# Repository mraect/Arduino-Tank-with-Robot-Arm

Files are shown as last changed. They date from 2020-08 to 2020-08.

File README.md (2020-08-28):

# Arduino Tank with Robot Arm 

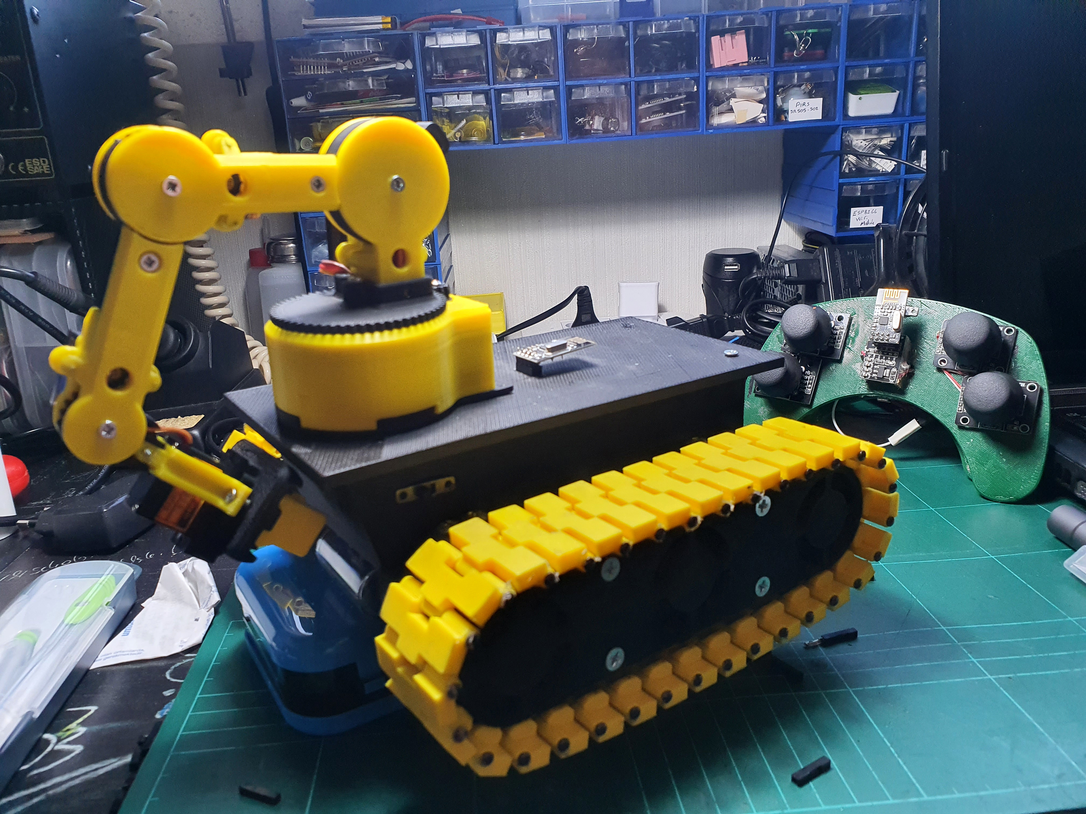
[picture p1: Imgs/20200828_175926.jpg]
ArduTankRobotArm


> For finished product photos, look "Imgs" folder.

# Needed Files;
  - For Robot Arm 3D files grab it from [Thingiverse - RobotArm3D][thingArm]
  - For Tank Threads 3D files grab it from [Thingiverse - Tank3D][thingTank]
  - For adapters and new chassis look "STL" folder
  - Code file look "Codes" folder
  - Need some sort of remote controller or raw Arduino attached nRF24L01 and some pots
  
  ### Folder Structure
  
| Folder | Description |
| --- | --- |
| Codes | Has 2 ino folder. One is for Main Arduino (KumandaAliciBasit) and other is for Robot Arm (RobotKolTekData)|
| Docs | PDF file which contains wiring diagram and explains data connection |
| Imgs | Images from finished project. Wiring photos, finished photos etc. |
| STL | 3D printer files which needed to make this project done |

# Needed Parts;
  - 2x Arduino Pro Mini
  - 4x DC geared Arduino motor
  - 5x 9g Servo (metal gear preferred)
  - 2x nRF24L01+ with breakout board
  - 3D printed files
  - Matek PDB or 12V to 5V buck converter (and more jumper wire)
  - M3 and M4 screws and nuts
  - 2mm x 30mm nails for treads
  - 2x Brushed ESC for tracks or one Brushed ESC which can control 2 motors separately.
  - 2S or 3S LiPo battery or 2 or 3 18650 LiIon battery
  - Jumper wires (female-female) to many of them :D
  - If you have 90° servos you need 2.2k resistors 2 for each servos

# Needed Tools;
  - Arduino IDE (v1.8.9 or higher) installed PC
  - 3D printer or slicing program fot STL files (Slic3r, Simple3D software etc.)
  - Screw driver
  - If you use PDB or you want to convert 90° servos to 180° servo, you need soldering iron
  - Hot glue gun for securing electronic parts
 
License
----

GNU GPLv3

[//]: # (These are reference links used in the body of this note and get stripped out when the markdown processor does its job. There is no need to format nicely because it shouldn't be seen. Thanks SO - http://stackoverflow.com/questions/4823468/store-comments-in-markdown-syntax)

   [thingTank]:<https://www.thingiverse.com/thing:972768>
   [thingArm]:<https://www.thingiverse.com/thing:2954381>

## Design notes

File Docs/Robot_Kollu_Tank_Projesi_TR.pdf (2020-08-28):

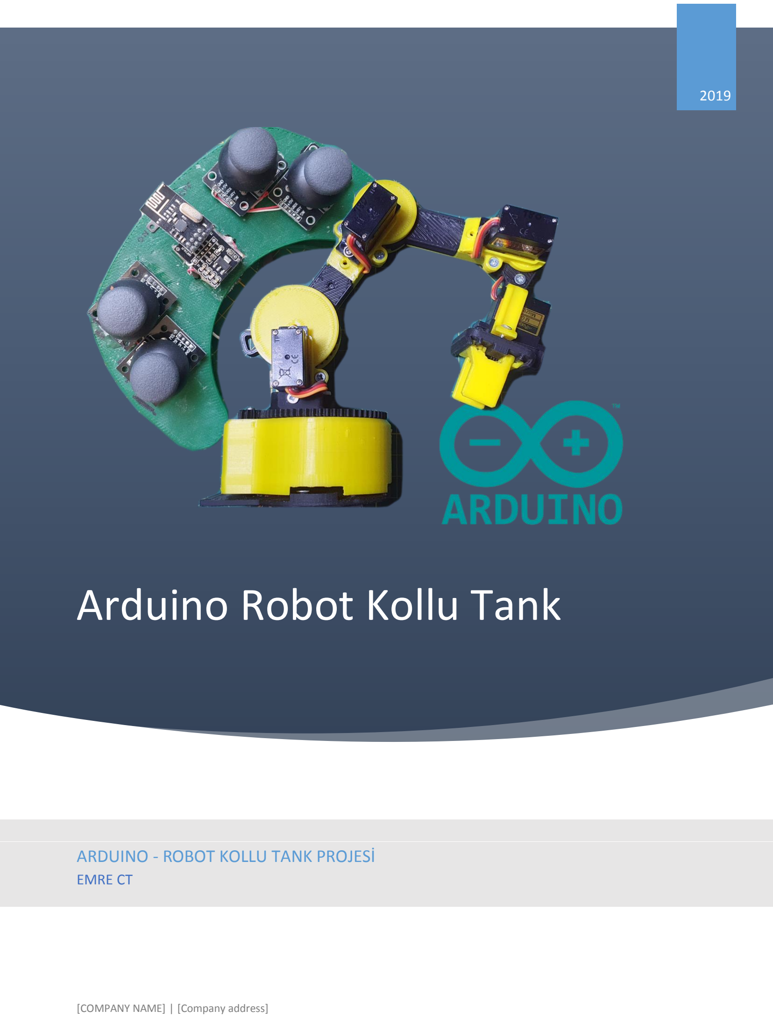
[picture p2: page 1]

# Arduino Robot Kollu Tank

2019

ARDUINO - ROBOT KOLLU TANK PROJESİ
EMRE CT
[COMPANY NAME] | [Company address]

Robot Kollu Tank Projesi

(Verici (Kumanda) Hariç)

## İçindekiler

Devre Elemanları

- 2x Arduino Pro Mini 5V/16Mhz
- 1x Matek PDB (Power Distribution Board) (Dahili 5V Buck Converterlı)
- 2x Brushless ESC
- 5x Servo 9g (MG90s Metal Gear)
- 1x NRF24L01+ Adaptör
- 1x NRF24L01+ Modül

Kısaltmalar

Ana Tank Kontrolörü Arduino Pro Mini (AR1 yada Main) (tankın önüne sabit olan Arduino)

Robot Kol Kontrolörü Arduino Pro Mini (AR2 yada Kol)

Brushless ESC (ESC)

nRF24L01+ (nRF)

Devre Şeması

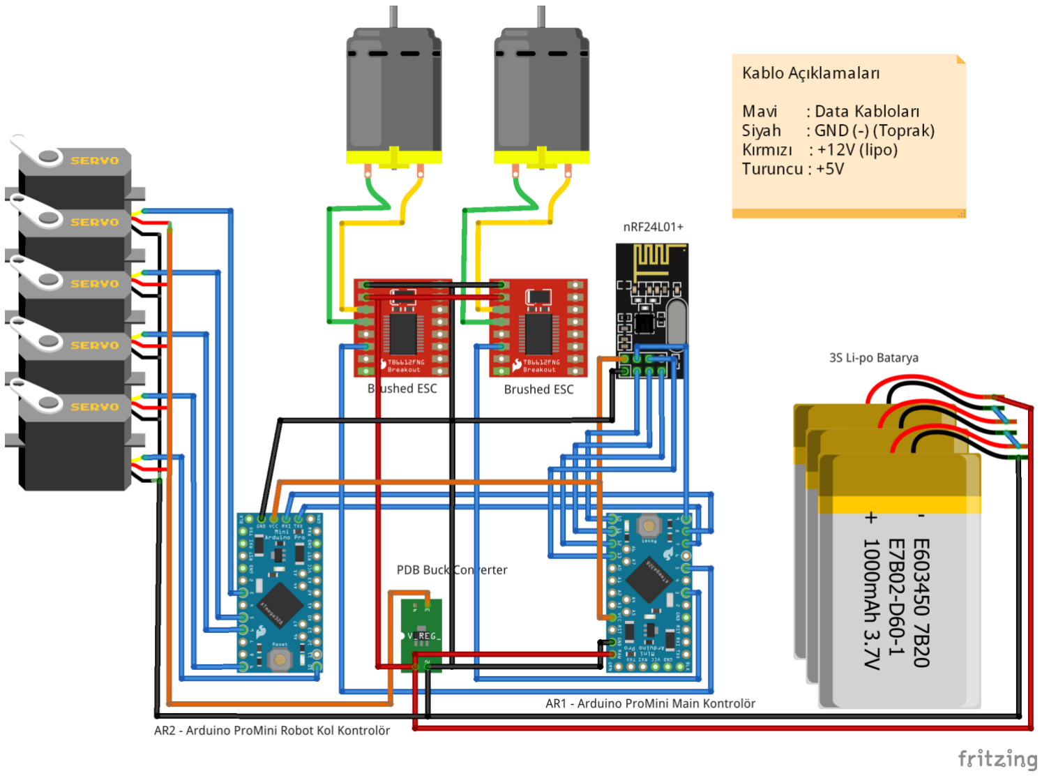
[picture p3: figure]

Bağlantı Açıklaması

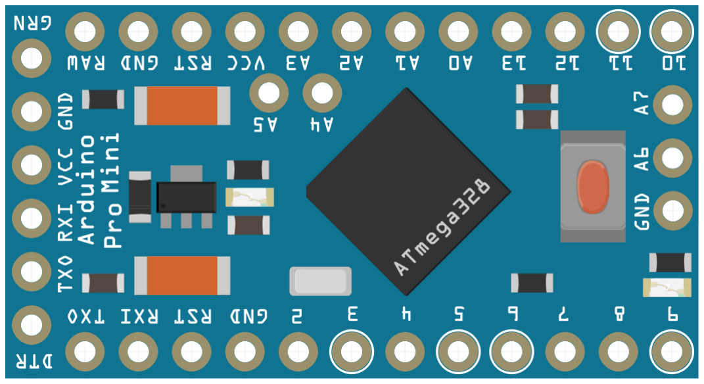
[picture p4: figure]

Bu AR1 (main kontrolör) aynı bu şekilde tankın ön duvarına yapışık durmaktadır.

1. PDB den çıkan 12V, 2 adet kablo ESC lere takılacak (kırmızı(+)-gri ve mavi(+)-beyaz)
2. Diğer 12V kablo (Gri-mor(+)) AR1 in RAW ve GND (Alttaki) pinine
3. nRF24L01 bağlantısı;
a. Mor(devamı beyaz) (CE) kablo AR1 in D10 pinine
b. Kahverengi (CSN) kablo AR1 in D9 pinine
c. Yeşil (SCK) kablo AR1 in D13 pinine
d. Mor (M0) kablo AR1 in D11 pinine
e. Mavi (M1) kablo AR1 in D12 pinine
f. Siyah kablo AR1 in GND (üstteki) pinine
g. Beyaz kablo AR1 in VCC (üstteki) pinine
4. ESC lerin sinyal kabloları AR1 in D3 ve D5 nolu pine
5. AR1 in D7 pinini AR2 nin TX0 pinine. AR1 in D8 pinini AR2 nin RX0 pinine
6. AR1 in VCC (soldaki) pinini AR2 nin VCC pinine, AR1 in GND (soldaki) pinini AR2 nin GND pinine.
7. Programlama için;
a. UEFI Kartının GND pini Main(AR1) veya Kol(AR2) GND pinine
b. UEFI Kartının 5V pini Main(AR1) veya Kol(AR2) 5V pinine
c. UEFI Kartının TXD pini Main(AR1) veya Kol(AR2) RX1 pinine
d. UEFI Kartının RXD pini Main(AR1) veya Kol(AR2) TX0 pinine
e. UEFI Kartının DTR pini Main(AR1) veya Kol(AR2) DTR pinine
8. Servoların Sinyal kabloları AR2 nin D3, D5, D6, D9, D10 pinlerine, Servoların VCC ve GND kabloları PDB deki 5V ve GND padine

Data Aktarım Sistemi;

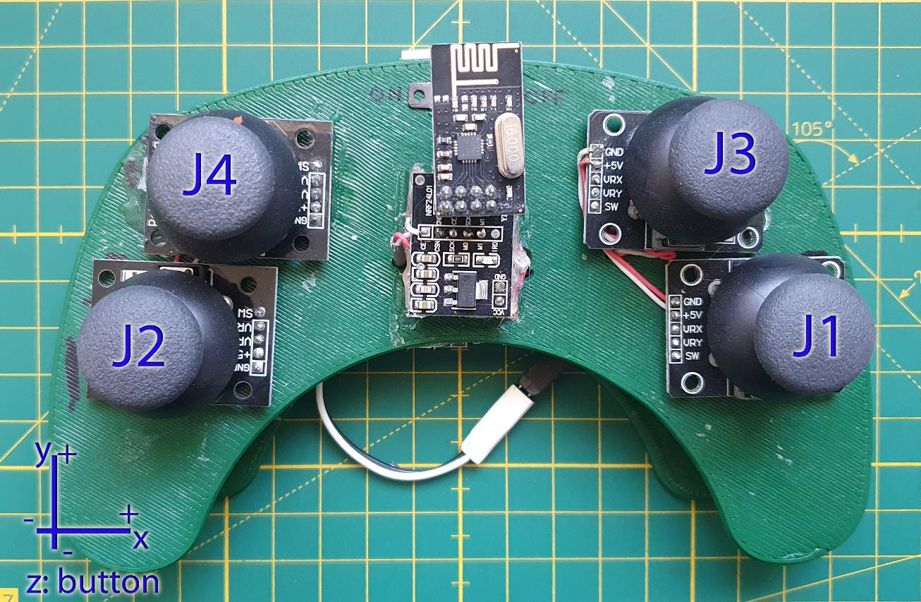
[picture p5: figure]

Aktarılan Veri;

493,513,504,508,512,516,510,515,0,0,0,0

Veri Kumanda Haritalaması;

Kumanda resminde belirtilen koordinat ve kodlara göre;

J1y (+0-1023), J1x (-0+1023), J2y (-0+1023), J2x (+0-1023),J3y (+0-1023), J3x (-0+1023), J4y (-0+1023), J4x (+0-1023), J4b (0:1), J2b (0:1), J1b (0:1), J3b (0:1)

Tank Haritalaması;

1 | 2 | 3 | 4 | 5 | 6 | 7 | 8 | 9 | 10 | 11 | 12
493, | 513, 504, 508, | 512, 516, 510, | 515, 0, | 0, | 0, | 0

Virgülle ayrılmış ilk 4 veriden 1. (J1y) ve 3. (J2y) veri tankın motorları için. 1. veri AR1 D3 pinine bağlı motor 3. veri AR1 D5 pinine bağlı motor için.

İlk 4 veriden sonraki veriler robot kol için AR1 (main) de ayıklanıp Robot Kol kontrolcüsüne aktarılır (AR2-Kol).

Robot Kol Haritalaması ve Kontrolü;

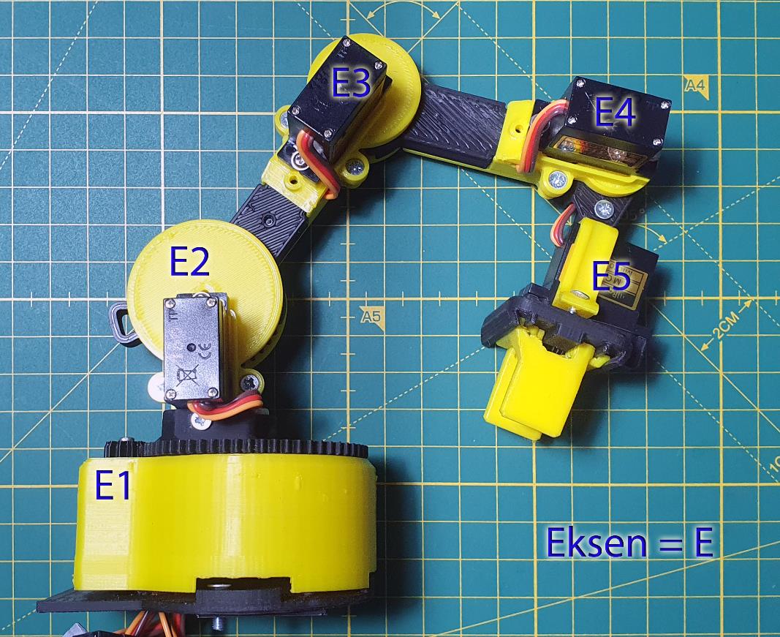
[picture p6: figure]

AR2 de D3 pinine bağlı servo E5 (Robot Kol Klipsi) eksenini kontrol eder. Bu kumandada “J4b” ile kontrol edilir. Bu sadece bir butondur ve açma/kapama işlemini yapar.

AR2 de D5 pinine bağlı servo E4 Eksenini kontrol eder. Bu kumandada “J4x” ile kontrol edilir.

AR2 de D6 pinine bağlı servo E3 Eksenini kontrol eder. Bu kumandada “J4y” ile kontrol edilir.

AR2 de D9 pinine bağlı servo E2 Eksenini kontrol eder. Bu kumandada “J3y” ile kontrol edilir.

AR2 de D10 pinine bağlı servo E1 Eksenini kontrol eder. Alt tablayı döndürmeye yarar. Bu kumandada “J3x” ile kontrol edilir.

Boş Veri ve Kontroller;

Veri alanında 2. , 4. , eksenler ve 10. , 11. , 12. Buton verileri boştadır bu alanlara daha sonra yazılımda eklemeler ile bir şeyler atanabilir.

Bu veri alanları kumandada J1x, J2x, J1b, J2b, J3b kontrollerine denk gelmektedir.

Arduino Kodları

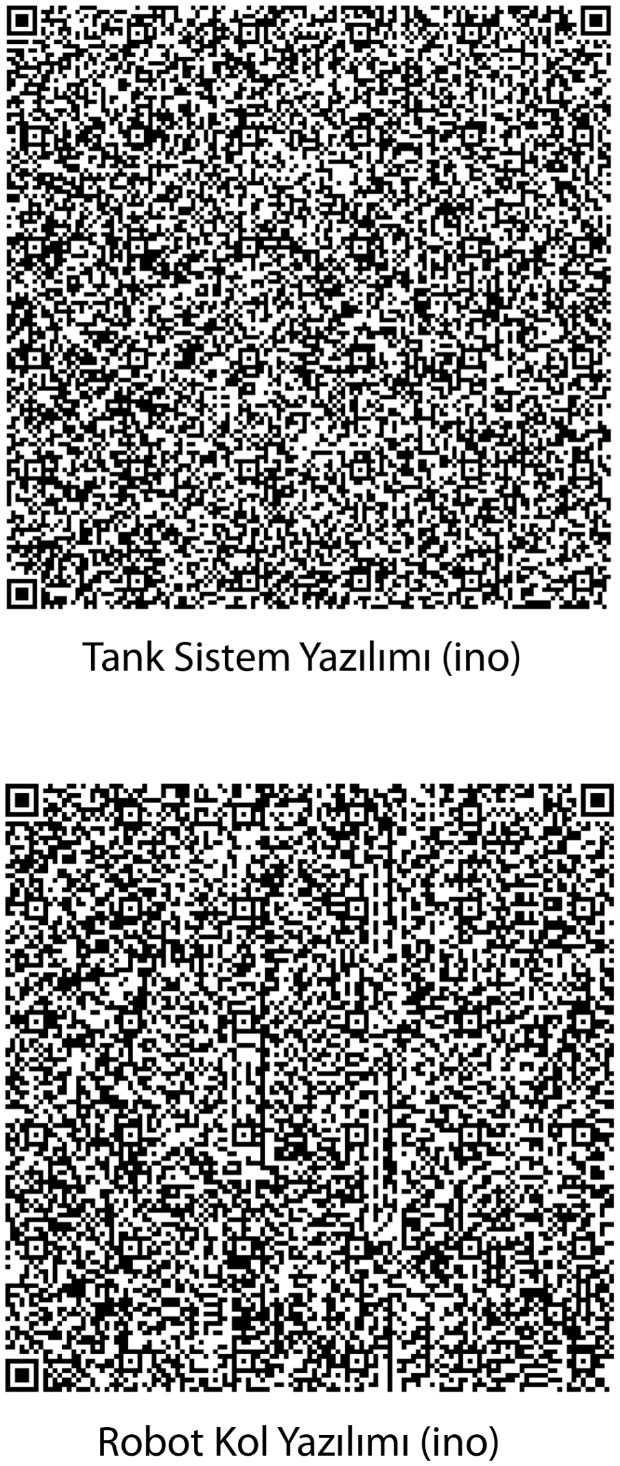
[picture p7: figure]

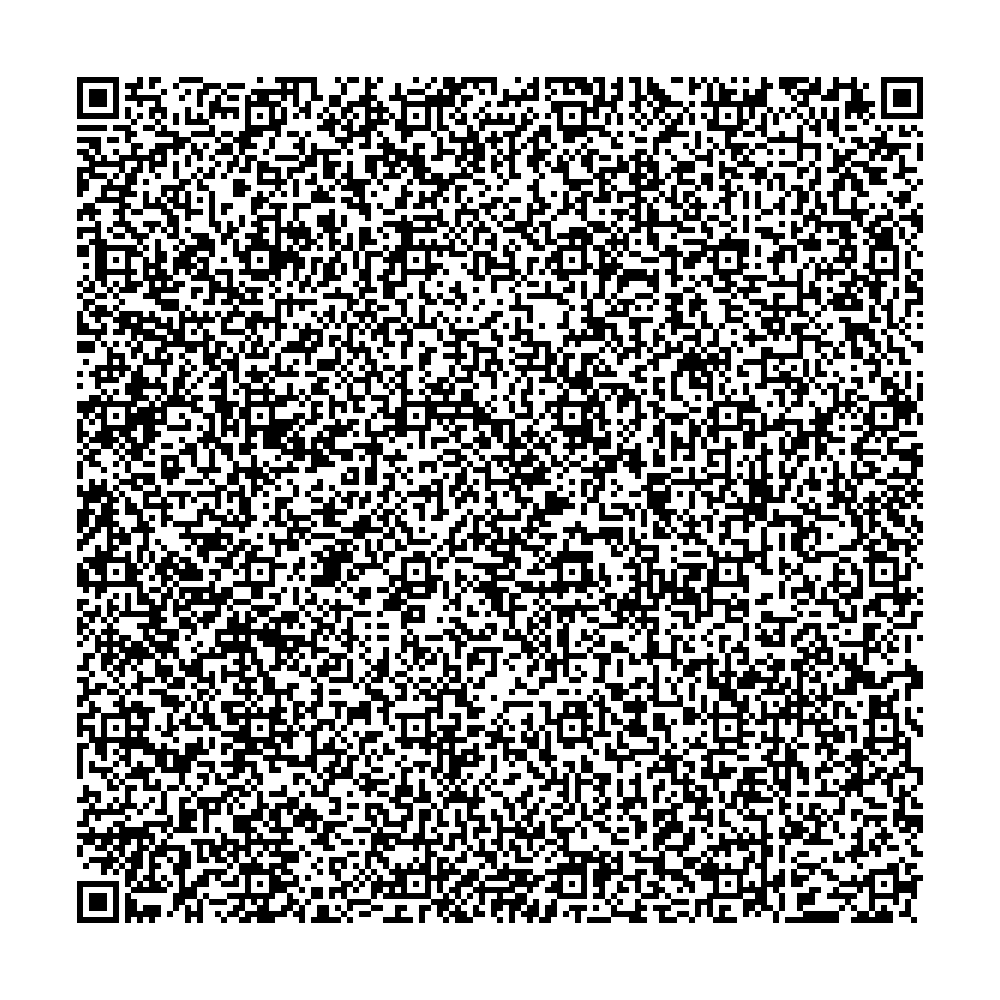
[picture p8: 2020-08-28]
Imgs/qrc_tankSistemi_ino.png

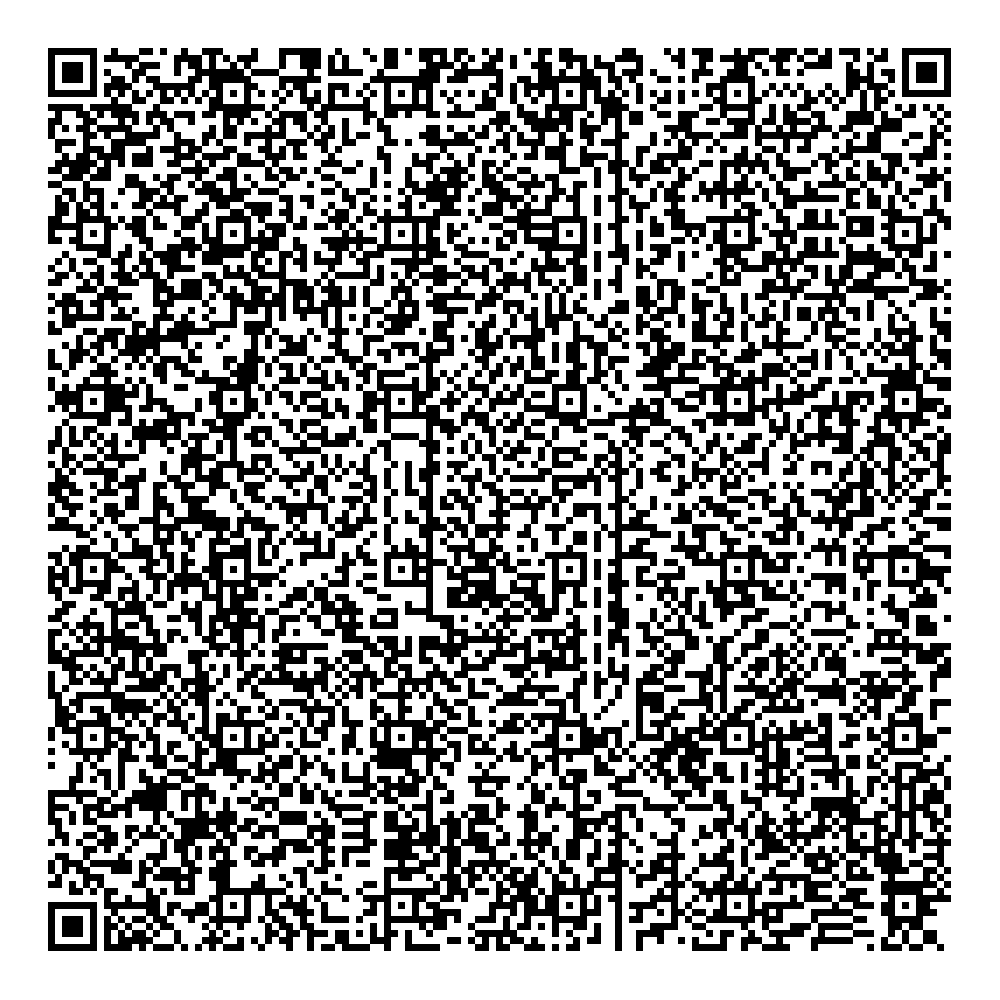
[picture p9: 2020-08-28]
Imgs/qrc_robotKol_ino.png

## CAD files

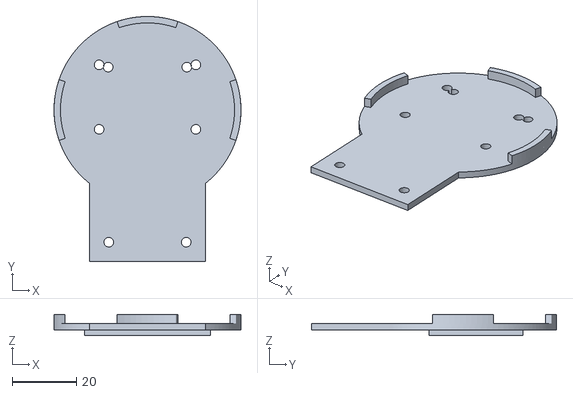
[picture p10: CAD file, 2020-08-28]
STL/robot arm to tank adapter.stl
58.0 x 76.0 x 6.60

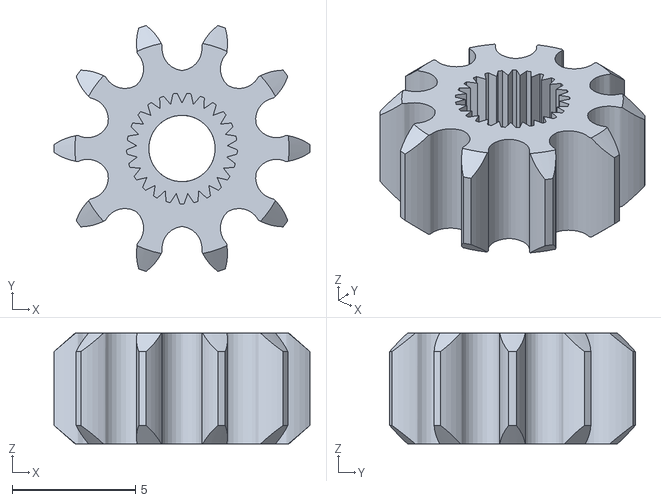
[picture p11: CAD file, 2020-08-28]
STL/gear for metal servo.stl
10.4 x 9.98 x 4.50

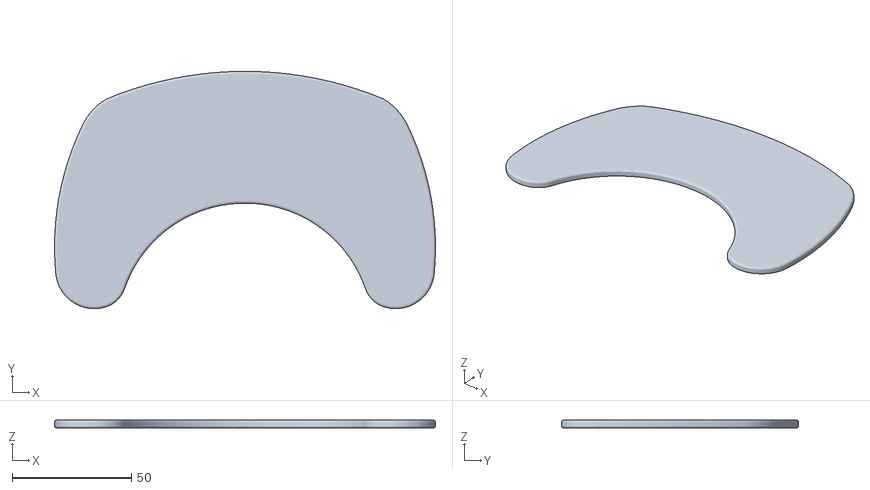
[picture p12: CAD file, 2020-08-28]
STL/remote top.stl
160.0 x 99.7 x 3.50

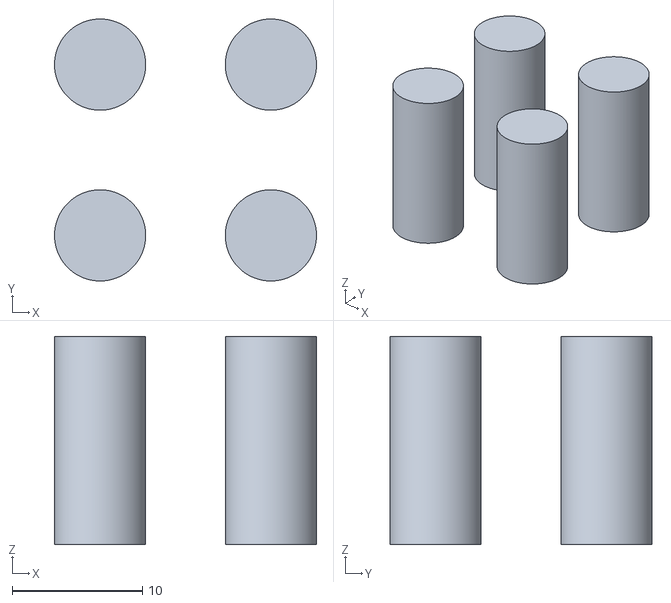
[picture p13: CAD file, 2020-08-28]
STL/remote spacers.stl
20.1 x 20.1 x 16.0

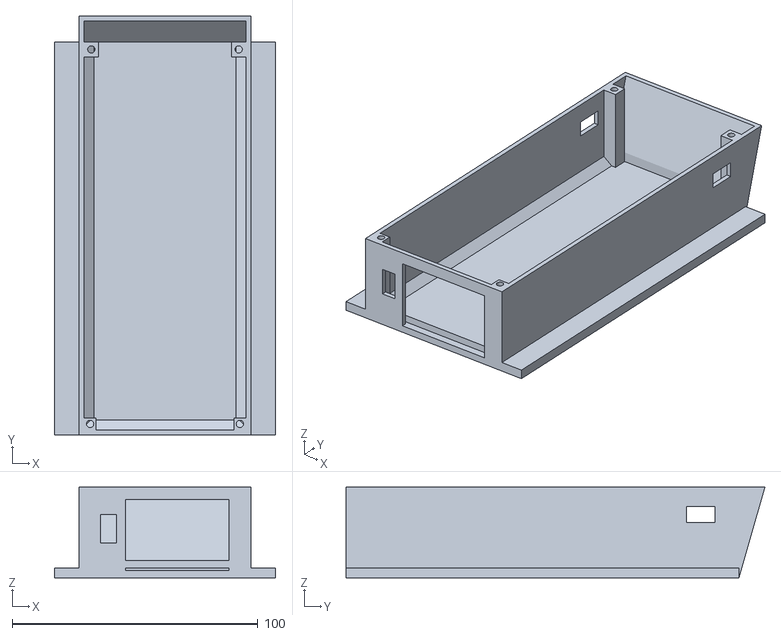
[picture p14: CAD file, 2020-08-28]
STL/tank new chassis.stl
90.0 x 170.6 x 37.0

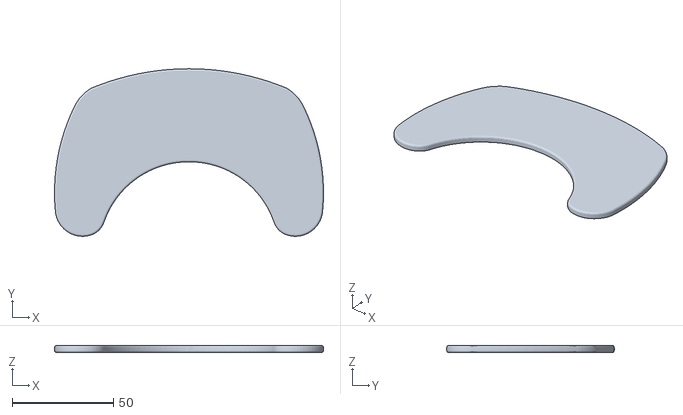
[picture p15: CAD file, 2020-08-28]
STL/remote bottom.stl
132.6 x 82.6 x 3.50

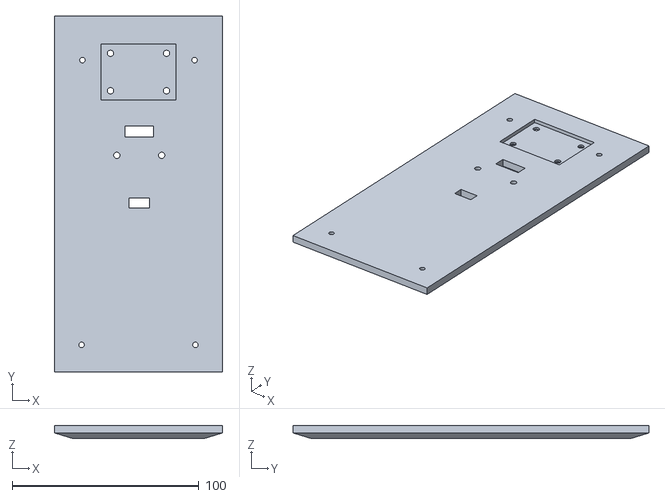
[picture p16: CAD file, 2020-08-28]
STL/tank platform.stl
90.0 x 190.6 x 7.00

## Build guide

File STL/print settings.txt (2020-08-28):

Material: 	PLA or ABS (ABS recommended)
Print Settings: 0.20 mm
Infill: 	20%

Support details;

No Support		gear for metal servo.stl
No Support		remote bottom.stl
No Support		remote spacers.stl
No Support		remote top.stl
Support on Plate	robot arm to tank adapter.stl
Support everywhere	tank new chassis.stl
Support on Plate	tank platform.stl (print up side down)

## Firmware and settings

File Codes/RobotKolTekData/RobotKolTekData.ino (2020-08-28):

#include <Servo.h>
Servo myservo1;
Servo myservo2;
Servo myservo3;
Servo myservo4;
Servo myservo5;

int minAngle=40;
int maxAngle=145;

void setup() {
  Serial.begin(38400);
  
  myservo1.attach(10); 
  myservo1.write(90);

  myservo2.attach(9); 
  myservo2.write(90);
  
  myservo3.attach(6); 
  myservo3.write(90);
  
  myservo4.attach(5); 
  myservo4.write(90);
  
  myservo5.attach(3); 
  myservo5.write(90);
}

// the loop function runs over and over again forever
void loop() {
  while (Serial.available() > 0) {
    int pos1 = Serial.parseInt();
    pos1 = (pos1 < minAngle ? minAngle : (pos1 > maxAngle ? maxAngle : pos1));
    
    int pos2 = Serial.parseInt();
    pos2 = (pos2 < minAngle ? minAngle : (pos2 > maxAngle ? maxAngle : pos2));
        
    int pos3 = Serial.parseInt();
    pos3 = (pos3 < minAngle ? minAngle : (pos3 > maxAngle ? maxAngle : pos3));
    
    int pos4 = Serial.parseInt();
    pos4 = (pos4 < minAngle ? minAngle : (pos4 > maxAngle ? maxAngle : pos4));
    
    int pos5 = Serial.parseInt();
    pos5 = (pos5 < minAngle ? minAngle : (pos5 > maxAngle ? maxAngle : pos5));
    
    Serial.println("Processing");
    
    int cache = Serial.read();
    if (cache == '\r' || cache == '\n')
    {
        myservo1.write(pos1); 
        myservo2.write(pos2); 
        myservo3.write(pos3); 
        myservo4.write(pos4); 
        myservo5.write(pos5); 
        
      delay(15);
      Serial.println("Servo Set");
    }
    delay(50);
  }
  delay(100);
}

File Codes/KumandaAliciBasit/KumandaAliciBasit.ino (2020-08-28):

#include <SPI.h>
#include "RF24.h"
#include <Servo.h>
#include <SoftwareSerial.h>

RF24 radio(10,9); //CE,CSN

Servo motorServo1;
Servo motorServo2;
SoftwareSerial sfSerial(7,8); //RX,TX

byte addresses[][6] = {"NRFTRX"};

uint16_t received_data[12] ;
uint8_t num_received_data = sizeof(received_data);

uint16_t roboKolData[5];

const int motorPin1 = 3;
const int motorPin2 = 5;

void setup() {
  Serial.begin(115200);
  sfSerial.begin(38400);

  motorServo1.attach(motorPin1);
  motorServo2.attach(motorPin2);
  
  radio.begin();
  radio.setPALevel(RF24_PA_MAX);
  
  radio.openReadingPipe(1,addresses[0]);
  radio.startListening();
  radio.printDetails();
}

int syc = 0;
void loop() {
    
    if (radio.available())
    {      
      syc++;
      radio.read( received_data, num_received_data);

      motorServo1.write(map((1023 - received_data[0]), 0, 1023, 0, 180));
      motorServo2.write(map(received_data[2], 0, 1023, 0, 180));

      roboKolData[4] = map(received_data[5], 0, 1023, 0, 180);
      roboKolData[3] = map((1023 - received_data[4]), 0, 1023, 0, 180);
      roboKolData[2] = map(received_data[6], 0, 1023, 0, 180);
      roboKolData[1] = map((1023 - received_data[7]), 0, 1023, 0, 180);
      roboKolData[0] = map(received_data[8], 1, 0, 30, 135);

      String data = "";
      
      for(int syc = 0; syc < 12 ; syc++)
        data += String(received_data[syc]) + ",";
        
      String data2 = "";
      for(int syc = 0; syc < 5 ; syc++)
        data2 += String(roboKolData[syc]) + ",";
        
      if(data2 != "")
        data2 = data2.substring(0,data2.length() - 1);

      if(syc % 14 == 0)
      {
        syc = 0;
        sfSerial.println(data2);
      }
      
      Serial.println(data);
    }
    
  delay(30);
}
